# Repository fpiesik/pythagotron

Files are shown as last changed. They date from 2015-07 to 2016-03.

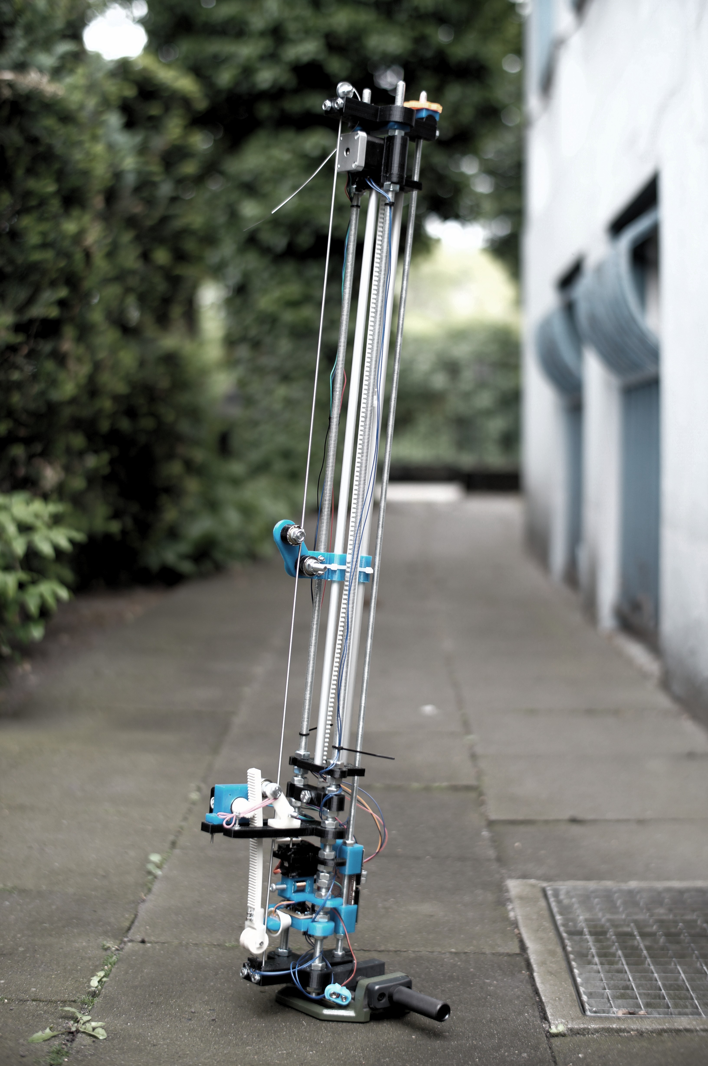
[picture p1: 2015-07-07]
doc/pictures/Pythagotron.jpg

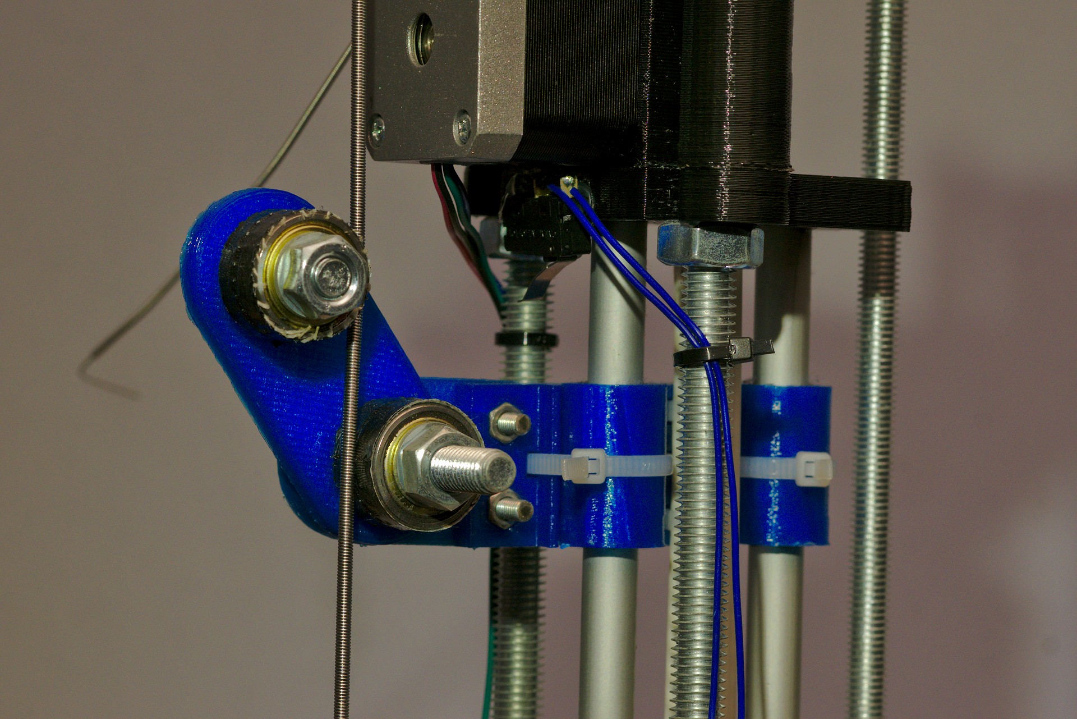
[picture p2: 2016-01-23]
doc/pictures/DSC03743.jpg

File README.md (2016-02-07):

Pythagoras of Samos was a man with many hobbys. I know him primarily for his experiments with strings and their musical properties. Thats why I call this robotic string instrument “Pythagotron”.

It features:

-2 octaves of pitch range
-fast and precise intonation
-4 actuators for striking, muting, punshing, damping and shorten the string
-modular and parametric design (OpenScad)
-most parts are 3D-printed or easy to gather
-open source

It's a parametric design made with OpenScad. You can view all the pieces put together by opening the file /print/pythagotron.scad. This preview differs a little from the actual way I put it together (see pictures).
To change the parameters, open /print/configuration.scad. You can also view or export every single piece by opening the corresponding .scad file and uncomment the module at the end of the file.

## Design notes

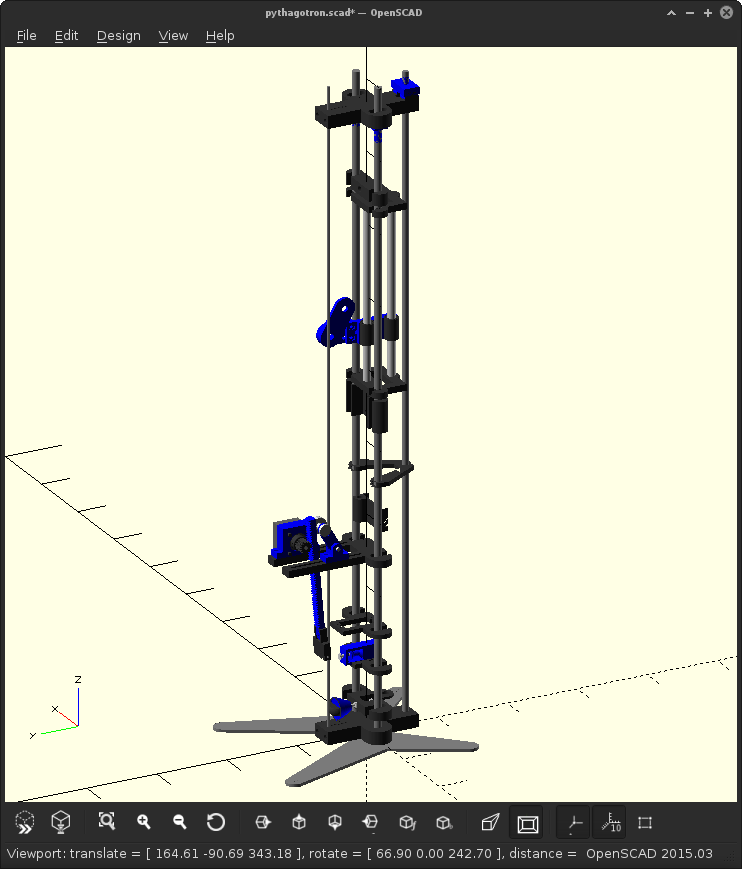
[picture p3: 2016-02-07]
doc/pictures/Screenshot_2016-01-23_19-48-24.png

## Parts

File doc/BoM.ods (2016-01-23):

Type | Specs | quant | price | Comment | Link
Frame
threaded rod | h=1m Ø=10mm | 2
threaded rod | h=1m Ø=8 | 1
threaded rod | h=14cm Ø=6mm | 4
rod | h=64cm Ø=10mm | 2
linear bearing | Ø=10 h=29mm | 2 |  | also available as printed part | http://www.igus.de/wpck/2292/drylin_r_rjum_01?ArtNr=RJUM-01-10&WT.mc_id=gadplDE022
bearing | Øi=8 Øo=22mm 608 Z (skateboard) | 6
Stepper motor | Nema17 | 1 |  |  | http://www.ebay.de/itm/DE-Ship-Nema-17-Schrittmotore-Stepper-Motor-Bipolar-59Ncm-CNC-3D-Printer-Reprap-/331440962687
Stepper motor | Nema14 | 1 |  |  | http://www.ebay.de/itm/Nema-14-Step-Motor-12V-0-4A-14Ncm-20oz-in-35x35x26mm-1-8deg-Bipolar-4-wire-/262038473998
Belt | T5 | ~2m |  |  | http://www.ebay.de/itm/Reprap-CNC-T5-PU-Zahnriemen-mit-Stahlzugstrang-T5-open-belt-/291357279515
Mainboard
Arduino nano |  | 1
Stepper motor driver | pololu a4988 or silent step stick (better) | 2 |  |  | http://www.watterott.com/de/SilentStepStick
DC-Converter | step down , 20V → 5-6V | 1 |  |  | http://www.ebay.de/itm/DC-DC-Schaltregler-Abwartswandler-LM2596HVS-4-5-53V-2A-step-down-converter-/321837441646
Power Jack | 5,5 mm / 2,1 mm | 1 |  |  | https://www.conrad.de/de/niedervolt-steckverbinder-buchse-einbau-horizontal-63-mm-21-mm-cliff-dc-10a-1-st-735742.html
Circuit Board | 100mm*50mm | 1 |  |  | https://www.conrad.de/de/basismaterial-fotobeschichtung-ohne-einseitig-35-m-l-x-b-100-mm-x-50-mm-106050-0100-proma-1-st-528200.html
Servo | standard | 1 |  |  | http://www.conrad.de/ce/de/product/275462/Bluebird-Standard-Servo-BMS-620-MG-Doppelt-kugelgelagert-Getriebe-Metall-JR
Mosfet | irf3205 | 2
Diode | 1n4001 | 2 |  |  | https://www.conrad.de/de/diode-1n4001-50v1a-diotec-1n4001-gehaeuseart-do-41-i-f-1-a-sperrspannung-u-r-50-v-162213.html
Kickup
copper wire | Coatet, Ø0,2mm | ~2m
Magnet | Neodym, Ø=5mm, h=min.20mm |  |  |  | https://www.conrad.de/de/piezokeramische-schallwandler-ft-serie-30-vac-4-05-khz-inhalt-1-st-710281.html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
 |  | 1 |  |  | http://www.supermagnete.de/stabmagnete-neodym-rund/stabmagnet-durchmesser-5mm-hoehe-25mm-neodym-n45-vernickelt_S-05-25-N
Preamp
opamp | tl081 | 1
trimpot
piezo | Ø27mm
Power Supply | ~20V, ~45W |  |  |  | https://www.conrad.de/de/notebook-netzteil-basetech-btna-90-90-w-15-vdc-16-vdc-195-vdc-462-a-1181511.html
Sring | Ø~0.1” (Low E-Bass-String) | 1

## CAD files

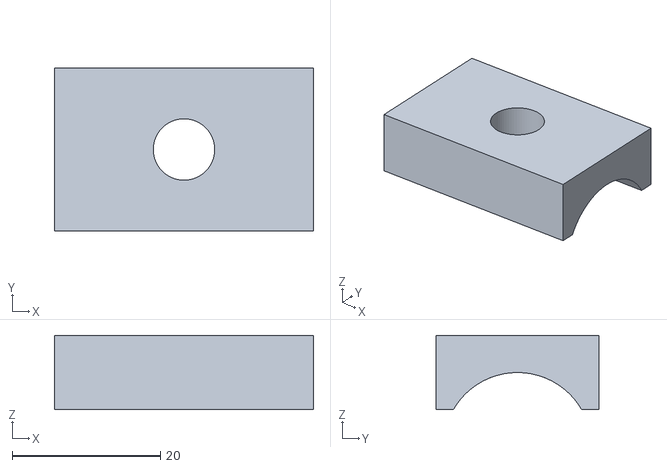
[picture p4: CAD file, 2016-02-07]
print/stls/tunerodfix.stl
35.0 x 22.0 x 10.0

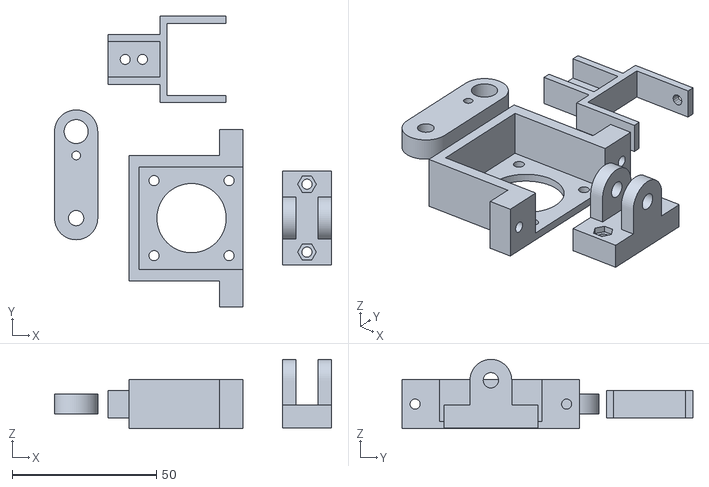
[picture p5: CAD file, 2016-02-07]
print/stls/damperB.stl
96.0 x 100.8 x 24.0

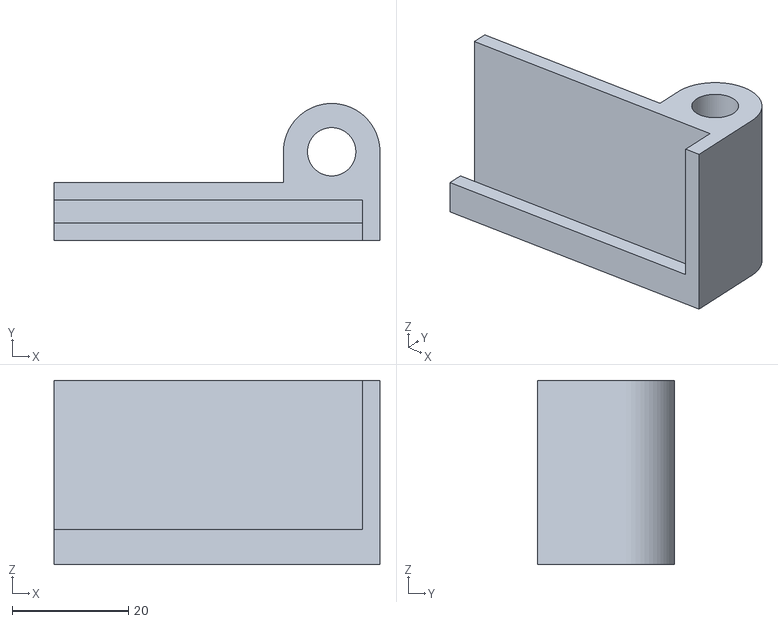
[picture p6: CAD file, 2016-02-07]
print/stls/pcb_mountA.stl
56.0 x 23.6 x 31.7

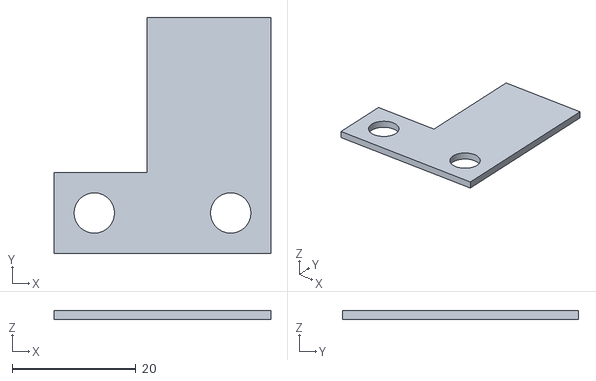
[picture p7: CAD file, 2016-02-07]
print/stls/endstop_mountB.stl
35.0 x 38.0 x 1.50

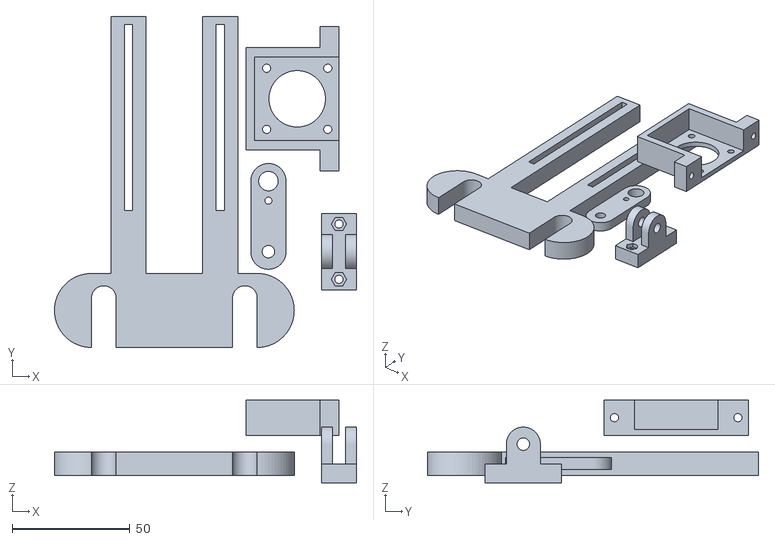
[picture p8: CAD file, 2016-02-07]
print/stls/damper.stl
128.5 x 140.8 x 35.2

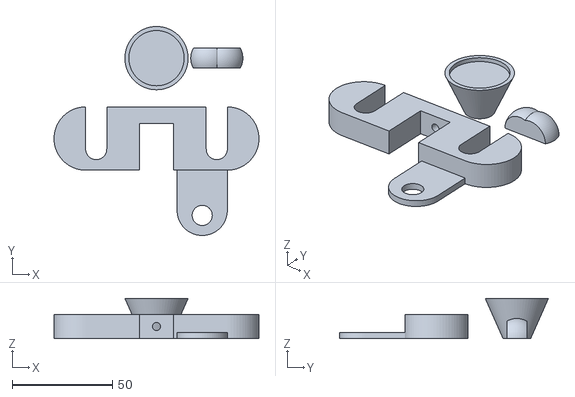
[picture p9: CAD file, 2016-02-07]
print/stls/piezo_pickup.stl
102.0 x 104.0 x 20.0

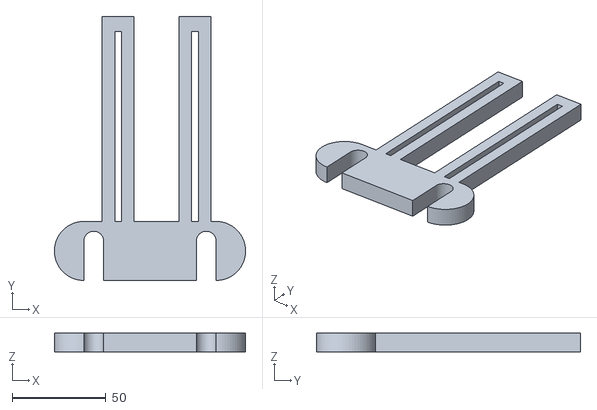
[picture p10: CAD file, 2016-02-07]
print/stls/damperA.stl
102.0 x 140.8 x 10.0

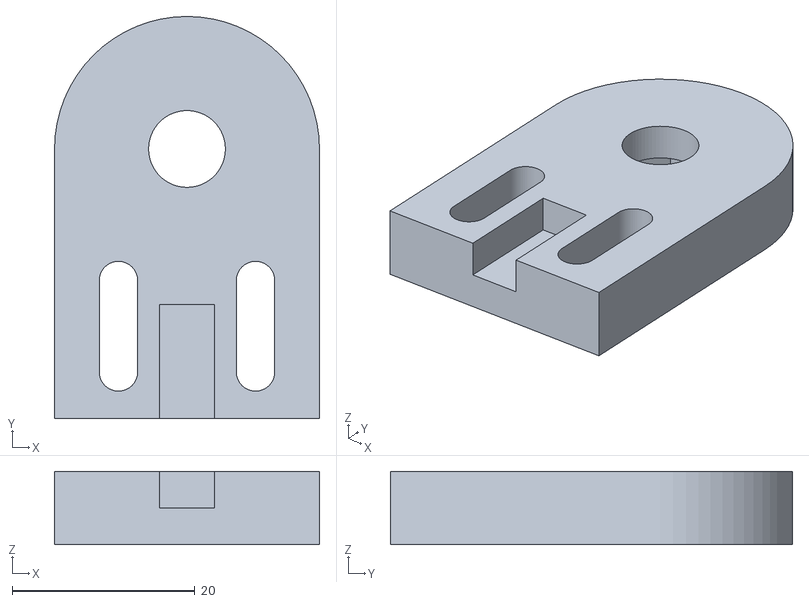
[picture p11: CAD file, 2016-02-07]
print/stls/stringshorter_armA.stl
29.0 x 44.0 x 8.00

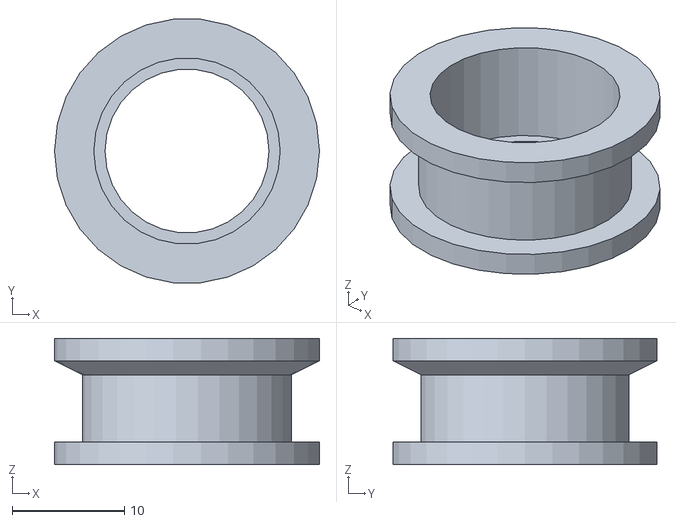
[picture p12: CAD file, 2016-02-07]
print/stls/pulleyB.stl
23.6 x 23.5 x 11.2

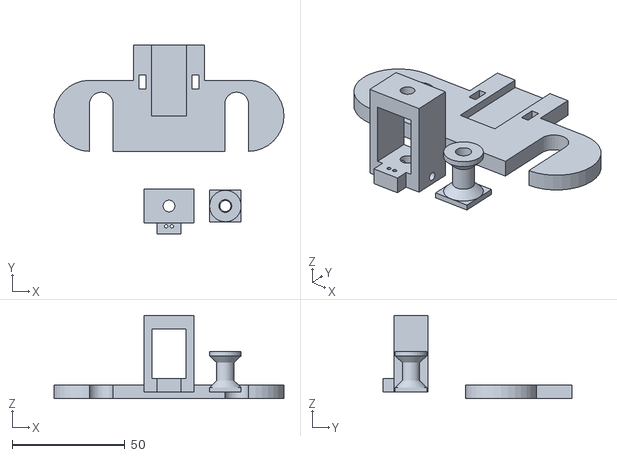
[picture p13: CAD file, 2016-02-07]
print/stls/kickup.stl
102.0 x 84.0 x 37.0

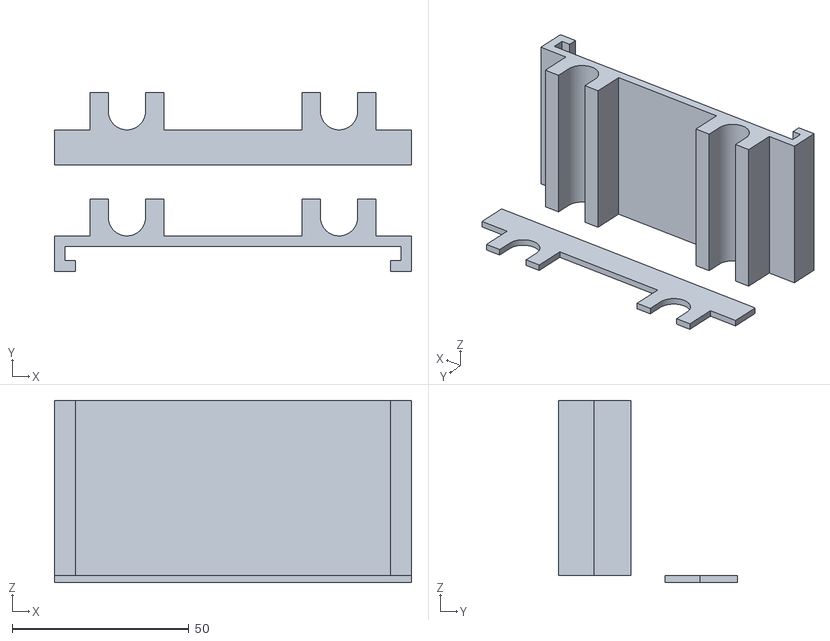
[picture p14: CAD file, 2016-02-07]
print/stls/pcb_mount.stl
101.0 x 50.5 x 51.5

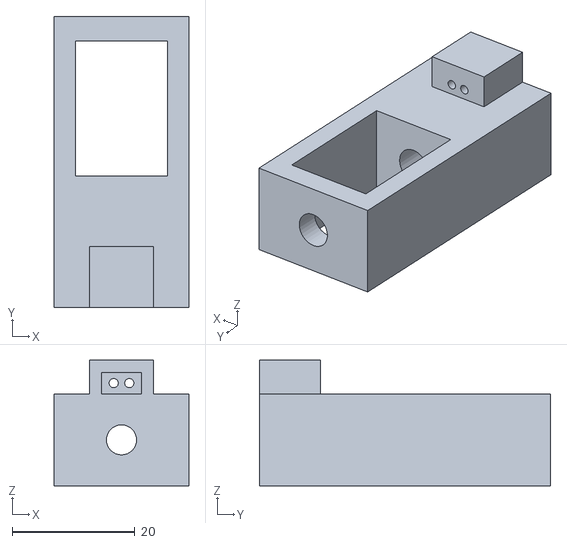
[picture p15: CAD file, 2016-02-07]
print/stls/kickup_A.stl
22.0 x 47.5 x 20.5

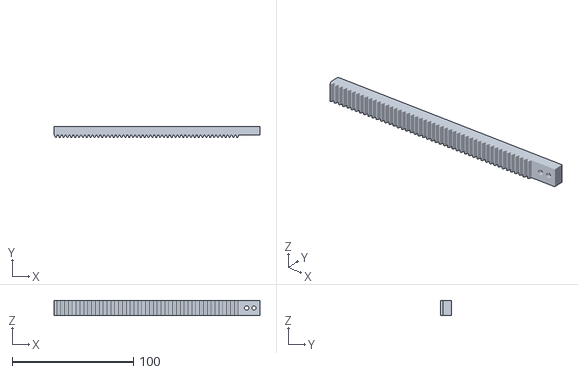
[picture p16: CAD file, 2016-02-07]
print/stls/damperC.stl
170.0 x 9.21 x 12.0

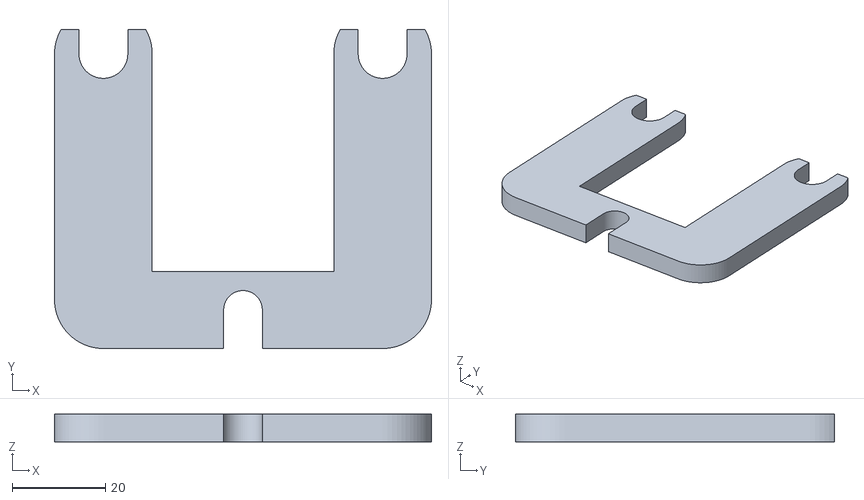
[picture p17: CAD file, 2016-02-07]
print/stls/spacer.stl
81.0 x 68.5 x 6.00

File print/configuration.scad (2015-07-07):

//Global variables: roddia, tunerodia, roddistance, screedlength, railroddia,stringholes


height=900; //overall height
roddia=10.5; //diameter of the main two rods
roddistance=60; //distance of the main two rods
tuneroddia=8.3; //diameter of the tunerod


pivotdia=20;
screedlength=130;
screedwidth=35;
screedheight=18;
stringroddist=screedlength-pivotdia;
stringdia=3.5;
stiffroddia=6.5;
pivotoffset=0;
stringholenumber=6;
stringholespread=5;

railrodZdist=20;
raildistance=35;
raildia=10.3;
railZ=250;



$fn=64;



basecolor=[0.2,0.2,0.2];    
actcolor=[0,0,1];

rodcolor=[0.5,0.5,0.5];
railcolor=[0.8,0.8,0.8];
boltcolor=[0.8,0.8,0.8];

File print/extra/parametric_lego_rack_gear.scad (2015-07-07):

width_in_studs  = 1;
teeth=48;
length= 170;
brick_height=7;
pocketZ=3.5;
screw_dia=3.5;
screw_posX=165;
screw_dist=6;

filz_mountX=18;
filz_dia=24;
filz_width=25;

  
  brick_width         = 12;
  stud_diameter       = 4.88;
 
  tooth_base_width    = 2.3;
  tooth_tip_width     = 0.87;
  tooth_height        = 2.06;
  tooth_top           = 5.79;
  tooth_tip_radius    = 0.15;
  teeth_per_brick     = 3.1;
  half_pegs_per_brick = 2;
  gap_width           = 0.884;



module tooth() {
  $fn = 20;
  

  //render()
  x_a = -((tooth_tip_width/2) - tooth_tip_radius);
  x_b = (tooth_tip_width/2) - tooth_tip_radius;
  translate([(gap_width+tooth_base_width)/2,0,-tooth_height+brick_height])
  rotate([0,0,180])
  translate([0,-(brick_width * width_in_studs)/2,tooth_height]) {
    difference() {
      hull() {
        translate([x_a,0,tooth_height]) rotate([90,0,0]) cylinder(r=tooth_tip_radius,   h=(brick_width * width_in_studs), center=true);
        translate([x_b,0,tooth_height]) rotate([90,0,0]) cylinder(r=tooth_tip_radius,   h=(brick_width * width_in_studs), center=true);
        translate([0,0,0])              rotate([90,0,0]) cylinder(r=tooth_base_width/2, h=(brick_width * width_in_studs), center=true);
      }
      translate([0,0,-1]) cube(size=[gap_width + tooth_base_width, brick_width * width_in_studs + 1, 1.9], center=true);
    }
  }
}

module rack() {
   wall_thickness      = 2;
difference(){
union(){
  tooth_width = tooth_base_width + gap_width;
  
 
  for ( i = [0 : teeth-1]) {
    translate([i * (tooth_base_width + gap_width), 0, 0]) tooth();
  }

  difference() {
    cube(size=[(length), (brick_width * width_in_studs), brick_height]);
    translate([wall_thickness,wall_thickness,0]) cube(size=[length - (wall_thickness*2), (brick_width * width_in_studs) - (wall_thickness*2), pocketZ]);
    // shave a bit off the beginning and end of the brick
    translate([-1.98,-1,0]) cube(size=[2, (brick_width * width_in_studs)+2, 10]);
    translate([length - 0.02,-1,0]) cube(size=[2,length+2, 10]);
  }

 }

translate([screw_posX,brick_width/2,0])cylinder(d=screw_dia, h=brick_height+1,$fn=16);
translate([screw_posX-screw_dist,brick_width/2,0])cylinder(d=screw_dia, h=brick_height+1,$fn=16);
}
}

module filz_mount(){
    wall_thickness      = 2.5;
    tolerance=0.3;
    height=brick_height+wall_thickness;
    block_rackY=filz_dia/2+3*wall_thickness+screw_dia;
    block_filzX=filz_dia/2+3*wall_thickness+screw_dia;
    block_filzY=filz_width+2*wall_thickness;
difference(){    
union(){
difference(){
cube([filz_mountX,brick_width+2*wall_thickness+tolerance,height],center=true);
translate([0,0,wall_thickness])cube([filz_mountX,brick_width+tolerance,height],center=true);    
}
difference(){
translate([filz_mountX/2+ block_filzX/2,0,0])cube([block_filzX,block_filzY,brick_height+wall_thickness],center=true); 
translate([filz_mountX/2+ block_filzX/2+wall_thickness,0,0])cube([block_filzX,filz_width,brick_height+wall_thickness],center=true); 
    }
}
translate([screw_dist/2,0,0])cylinder(d=screw_dia, h=brick_height+wall_thickness+1,$fn=16,center=true);
translate([-screw_dist/2,0,0])cylinder(d=screw_dia, h=brick_height+wall_thickness+1,$fn=16,center=true);
translate([filz_mountX/2+block_filzX-screw_dia/2-wall_thickness,0,0])rotate([90,0,0])cylinder(d=screw_dia, h=filz_width+2*wall_thickness+1,$fn=16,center=true);
}
}

//rack();
filz_mount();

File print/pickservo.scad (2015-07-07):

include <configuration.scad>;

module pickservo_mount(){

height=6;
depth=roddia*3;
width=roddistance+roddia;
screwdia=3;
screwnumber=2; //one or two screws
screwdistance=10; //if two screws
servowidth=40.5;
servodepth=20.5;
servosupportX=8;
servosupportY=8;

cable_cutoutX=5;
cable_cutoutY=3;

offsetY=15;

rotate([0,0,0]){
difference(){
union(){


cube([width,depth,height],center=true);
translate([width/2,0,0]){
cylinder(d=depth,h=height,center=true);}
translate([-width/2,0,0]){
cylinder(d=depth,h=height,center=true);}
translate([0,offsetY,0]){
cube([servodepth+servosupportX*2,servowidth+servosupportY*2,height],center=true);
}}
translate([0,offsetY,0]){
cube([servodepth,servowidth,height+1],center=true);
cube([cable_cutoutX,servowidth+cable_cutoutY*2,height+1],center=true);

if (screwnumber==1){
translate([0,servowidth/2+servosupportY/2,0]){
cylinder(d=screwdia,h=height+1,center=true);}
translate([0,-(servowidth/2+servosupportY/2),0]){
cylinder(d=screwdia,h=height+1,center=true);}
}

if (screwnumber==2){
translate([screwdistance/2,0,0]){
translate([0,servowidth/2+servosupportY/2,0]){
cylinder(d=screwdia,h=height+1,center=true);}
translate([0,-(servowidth/2+servosupportY/2),0]){
cylinder(d=screwdia,h=height+1,center=true);}
}
translate([-screwdistance/2,0,0]){
translate([0,servowidth/2+servosupportY/2,0]){
cylinder(d=screwdia,h=height+1,center=true);}
translate([0,-(servowidth/2+servosupportY/2),0]){
cylinder(d=screwdia,h=height+1,center=true);}
}
}

}

translate([0,depth/2-roddia,0]){
translate([roddistance/2,0,0]){
cylinder(d=roddia,h=height+1,center=true);}
translate([-roddistance/2,0,0]){
cylinder(d=roddia,h=height+1,center=true);}

translate([roddistance/2,-depth/2,0]){
cube([roddia,depth,roddia],center=true);}
translate([-roddistance/2,-depth/2,0]){
cube([roddia,depth,roddia],center=true);}
}

}

}
}
//servo_mount();

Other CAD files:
print/stls/rail_mount.stl
print/stls/pcb_mountB.stl
print/stls/picker.stl
print/stepper_mount.scad
print/damper.scad
print/endmounts.scad
print/endstop_mount.scad
print/extra/bearing.scad
print/extra/bolt_nut.scad
print/extra/legopulley.scad
print/extra/linear_bearing.scad
print/extra/nema.scad
print/extra/pulleyA.scad
print/extra/pulleyB.scad
print/extra/rack_gear.scad
print/kickup.scad
print/pcb_mount.scad
print/pick.scad
print/picker.scad
print/pickup_mag.scad
print/piezo_pickup.scad
print/pulley_mount.scad
print/pythagotron.scad
print/rack_gear.scad
print/rail_mount.scad
print/spacer.scad
print/stand.scad
print/stls/endstop_mount.stl
print/stls/kickup_C.stl
print/stls/kickup_D.stl
print/stls/pivot.stl
print/stls/pulleyA.stl
print/stls/pulleymount.stl
print/stls/screedA.stl
print/stls/screedB.stl
print/stls/stand.stl
print/stls/steppermountA.stl
print/stls/stringshorter.stl
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

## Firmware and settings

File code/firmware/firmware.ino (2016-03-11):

#include <Servo.h>
Servo servo1;
Servo servo2;

const int home1_pin = 13;  //Digital input 1
const int home2_pin = 12;  //Digital input 2

//-------choose hardware---------------------
//uncomment if Hardware V1
const int analogAux1_pin = A6;
const int analogAux2_pin = A7;
const int step1_stpPin = 3;
const int step1_dirPin = 2;
const int step1_enblPin = 4;
const int step2_stpPin = 6; 
const int step2_dirPin = 5;
const int step2_enblPin = 7;

//uncomment if hardware V2
//const int analogAux1_pin = A0;// A6 Hardware ref1
//const int analogAux2_pin = A1;// A7  "
//const int step1_stpPin = 3;
//const int step1_dirPin = 4; 
//const int step1_enblPin = 2;
//const int step2_stpPin = 6;
//const int step2_dirPin = 7;  
//const int step2_enblPin = 5; 
//--------------------------------------------

const int mosfet1_pin = 10; 
const int mosfet2_pin = 11;

const int servo1Pin = 9;
const int servo2Pin = 8;



bool step1_enbl=0;
int step1_maxSpd = 240; 
int step1_homeSpd = 800; 
long step1_startSpd = 10000;
long step1_brkSteps = 100;
int step1_rampAmnt = 5;
bool step1_rmpDwn = 0;
bool step1_rmpUp = 0;
int step1_trgtSpd = 1500;
byte step1_dir = 0;
byte step1_move = 0;
long step1_pos=0;
long  step1_trgt;
long step1_prevTrgt;
long step1_trgtA;
long step1_trgtB;
bool step1_arrvd=1;
long step1_interval = 1000; 
unsigned long step1_prvMilli = 0; 
byte step1_homeState = 1;
byte step1_arriving=0;
long step1_prevPos;


bool step2_enbl=0;
int step2_maxSpd = 240; 
int step2_homeSpd = 1200; 
long step2_startSpd = 5000;
long step2_brkSteps = 50;
int step2_rampAmnt = 5;
bool step2_rmpDwn = 0;
bool step2_rmpUp = 0;
int step2_trgtSpd = 1500;
byte step2_dir = 0;
byte step2_move = 0;
long step2_pos=0;
long  step2_trgt;
long step2_prevTrgt;
long step2_trgtA;
long step2_trgtB;
bool step2_arrvd=1;
long step2_interval = 1000; 
unsigned long step2_prvMilli = 0; 
byte step2_homeState = 1;
byte step2_arriving=0;
long step2_prevPos;


unsigned int kick1_duration;
unsigned long kick1_prvMilli = 0;
unsigned long kick1_currMilli = 0;  

unsigned int kick2_duration;
unsigned long kick2_prvMilli = 0;
unsigned long kick2_currMilli = 0;  

int servo1_strtPos = 90;
int servo2_strtPos = 90;


byte serbyte = 0;
byte incoming = 0;





void step_home(byte stepper){
  byte home_pin;
  byte enbl_pin;
  byte dir_pin;
  byte stp_pin;
  int home_spd;
  
    
  if (stepper==1){
    home_pin= home1_pin;
    enbl_pin = step1_enblPin;
    dir_pin = step1_dirPin;
    stp_pin = step1_stpPin;
    home_spd = step1_homeSpd;
    step1_pos=0;
     
  }
  
   if (stepper==2){
    home_pin= home2_pin;
    enbl_pin = step2_enblPin;
    dir_pin = step2_dirPin;
    stp_pin = step2_stpPin;
    home_spd = step2_homeSpd;
    step2_pos=0;
 
  }
  
  stepDir(stepper,1); 
  
      
  while (digitalRead(home_pin)==1){
  digitalWrite(enbl_pin, LOW);
  digitalWrite(stp_pin, HIGH);
  delayMicroseconds(10);
  digitalWrite(stp_pin,LOW);
  delayMicroseconds(home_spd-10);
  }
  //digitalWrite(enblPin, HIGH);
  //digitalWrite(enbl_pin, HIGH);
  stepSndpos(stepper);
  
}





void mosfet(byte mosfet,byte time){
  if(mosfet==1){
  digitalWrite (mosfet1_pin,HIGH);
  kick1_prvMilli = kick1_currMilli;  
  kick1_duration = time;
  } 
   if(mosfet==2){
  digitalWrite (mosfet2_pin,HIGH);
  kick2_prvMilli = kick2_currMilli;  
  kick2_duration = time;
  } 
}

//------------------------------------------------------------------------    
void stepEnbl(byte stepper,int state){
 byte enbl_pin;
 
 if (stepper==1) enbl_pin=step1_enblPin;
 if (stepper==2) enbl_pin=step2_enblPin;
 
 int statePin=state*-1+1;
 digitalWrite(enbl_pin, statePin);
 
 if (stepper==1)  step1_enbl=state;
 if (stepper==2)  step2_enbl=state;
 delayMicroseconds(50);
}

//------------------------------------------------------------------------
void stepDir(byte stepper,byte dir){
  byte step_dir;
  byte dir_pin;
  
  if (stepper == 1){
  step_dir=step1_dir;
  dir_pin = step1_dirPin;
  }
  if (stepper == 2){
  step_dir=step2_dir;
  dir_pin = step2_dirPin;
  }
  if(step_dir!=dir){
  digitalWrite(dir_pin, dir);
  
  
  if (stepper==1)step1_dir=dir;
  if (stepper==2)step2_dir=dir;
  delayMicroseconds(2); 
  }
}
//-------------------------------------------------------------------------
void step_setSpd(byte stepper,long spd){
  if(stepper==1){
    step1_trgtSpd= step1_maxSpd+100*step1_startSpd/(spd+100)-100*step1_startSpd/300;
    step1_rmpUp=1;
    
  }
  
  if(stepper==2){
    step2_trgtSpd= step2_maxSpd+100*step2_startSpd/(spd+100)-100*step2_startSpd/300;
    step2_rmpUp=1;
   }
   
   
}
//-------------------------------------------------------------------------
void stepSndpos(byte stepper){
  long step_pos;
  
  if(stepper==1)step_pos=step1_pos;
  if(stepper==2)step_pos=step2_pos;
  
  long pos1=step_pos/1000;
  long pos2=(step_pos-pos1*1000)/10;
  long pos3=step_pos-pos1*1000-pos2*10;
  if(stepper==1)Serial.write(255);
  if(stepper==2)Serial.write(254);
  Serial.write(pos1);
  Serial.write(pos2);
  Serial.write(pos3);
}


//-------------------------------------------------------------------------
void stepMove(byte stepper){
  
unsigned long prvMilli;
long interval;
byte stp_pin;
byte dir;
long pos;
long prev_pos;
long trgt;
int brkSteps;
byte rmpUp;
byte rmpDwn;
byte arriving;
int trgtSpd;
long startSpd;

if (stepper==1){
  prvMilli=step1_prvMilli;
  interval=step1_interval;
  stp_pin=step1_stpPin;
  dir=step1_dir;
  pos=step1_pos;
  trgt=step1_trgt;
  brkSteps=step1_brkSteps;
  rmpUp=step1_rmpUp;
  rmpDwn=step1_rmpDwn;
  arriving=step1_arriving;
  prev_pos=step1_prevPos;
  trgtSpd=step1_trgtSpd;
  startSpd=step1_startSpd;
  
}

if (stepper==2){
  prvMilli=step2_prvMilli;
  interval=step2_interval;
  stp_pin=step2_stpPin;
  dir=step2_dir;
  pos=step2_pos;
  trgt=step2_trgt;
  brkSteps=step2_brkSteps;
  rmpUp=step2_rmpUp;
  rmpDwn=step2_rmpDwn;
  arriving=step2_arriving;
  prev_pos=step2_prevPos;
  trgtSpd=step2_trgtSpd;
  startSpd=step2_startSpd;
}
  
  unsigned long currentMillis = micros();
  if(currentMillis - prvMilli >= interval) {
      
  digitalWrite(stp_pin, HIGH);
  delayMicroseconds(4);
  digitalWrite(stp_pin,LOW);
  if(dir==0)pos=pos+1;
  if(dir==1)pos=pos-1;
  if((sqrt(pow(pos - trgt,2))<brkSteps) && (sqrt(pow(pos - trgt,2))<sqrt(pow(prev_pos - trgt,2)))){
  interval = interval + 2*brkSteps / sqrt(pow(pos - trgt,2));
  //stepRmpdwn(stepper,(startSpd-trgtSpd)/brkSteps);
  arriving=1;}  
  
  prev_pos=pos;
  
  if (stepper==1){
  step1_prvMilli = currentMillis; 
  step1_pos=pos;
  step1_prevPos=prev_pos;
  step1_arriving=arriving;
  step1_interval=interval;
  }
  if (stepper==2){
  step2_prvMilli = currentMillis; 
  step2_pos=pos;
  step2_prevPos=prev_pos;
  step2_arriving=arriving;
  step2_interval=interval;
  }

  }
  
  
}
//--------------------------------------------------------------------------
void stepGo2pos(byte stepper){
  long trgt;
  long prevTrgt;
  byte trgtA;
  byte trgtB;
  byte rmpUp;
  byte rmpDwn;
  long pos;
  bool arrvd;
 
 
 if(stepper==1){
  trgt=step1_trgt;
  prevTrgt=step1_prevTrgt;
  trgtA=step1_trgtA;
  trgtB=step1_trgtB;
  rmpUp=step1_rmpUp;
  rmpDwn=step1_rmpDwn;
  pos=step1_pos;
  arrvd=step1_arrvd;
  
 }
  if(stepper==2){
  trgt=step2_trgt;
  prevTrgt=step2_prevTrgt;
  trgtA=step2_trgtA;
  trgtB=step2_trgtB;
  rmpUp=step2_rmpUp;
  rmpDwn=step2_rmpDwn;
  pos=step2_pos;
  arrvd=step2_arrvd;
 }
 
  
  rmpUp=1;
  trgt=trgtA*100+trgtB;
  if (trgt!=pos) {
  arrvd=0;
  
  if(prevTrgt>pos && trgt<pos)rmpDwn=1;
  if(prevTrgt<pos && trgt>pos)rmpDwn=1;
  
  prevTrgt=trgt;}
  
  if(stepper==1){
  step1_trgt=trgt;  
  step1_prevTrgt=prevTrgt;
  step1_rmpUp=rmpUp;
  step1_rmpDwn=rmpDwn;
  step1_arrvd=arrvd;
  step1_arriving=0;
  }
   if(stepper==2){
  step2_trgt=trgt;
  step2_prevTrgt=prevTrgt;
  step2_rmpUp=rmpUp;
  step2_rmpDwn=rmpDwn;
  step2_arrvd=arrvd;
  step2_arriving=0;
  }
  
}
//------------------------------------------------------------------------------
void stepRmpdwn(byte stepper,int amount){
  long startSpd;
  long interval;
  byte rmpDwn;
   
  if (stepper==1) {
  startSpd=step1_startSpd;
  interval=step1_interval;
  rmpDwn=step1_rmpDwn;
  }
  
  if (stepper==2) {
  startSpd=step2_startSpd;
  interval=step2_interval;
  rmpDwn=step2_rmpDwn;
  }
  
  if(startSpd>interval)interval=interval+amount;
  if(startSpd<interval)interval=interval-amount;
  if(startSpd<=interval+amount && startSpd>=interval-amount)rmpDwn=0;
  
  if (stepper==1){
  step1_rmpDwn=rmpDwn;
  step1_interval=interval;
  }
  if (stepper==2){
  step2_rmpDwn=rmpDwn;
  step2_interval=interval;
  }
  
  
  
  
  }

//--------------------------------------------------------------------------------
void stepRmpup(byte stepper){
  
  int trgtSpd;
  long interval;
  int rampAmnt;
  byte rmpUp;
  byte arriving;
   
  if (stepper==1) {
  trgtSpd=step1_trgtSpd;
  interval=step1_interval;
  rampAmnt=step1_rampAmnt;
  rmpUp=step1_rmpUp;
  arriving=step1_arriving;
  }
   if (stepper==2) {
  trgtSpd=step2_trgtSpd;
  interval=step2_interval;
  rampAmnt=step2_rampAmnt;
  rmpUp=step2_rmpUp;
  arriving=step2_arriving;
  }
  
  if(rmpUp==1 && arriving==0){
  if(trgtSpd>interval)interval=interval+rampAmnt;
  if(trgtSpd<interval)interval=interval-rampAmnt;}
  if(trgtSpd<=interval+rampAmnt && trgtSpd>=interval-rampAmnt)rmpUp=0;
  
  if (stepper==1){
  step1_rmpUp=rmpUp;
  step1_interval=interval;}
  
  if (stepper==2){
  step2_rmpUp=rmpUp;
  step2_interval=interval;}
  
}

void setServo(byte servo,byte pos){
if (servo==1 && pos!=0){
  servo1.attach(servo1Pin);
  servo1.write(pos);
 }
if (servo==2 && pos!=0){
  servo2.attach(servo2Pin);
  servo2.write(pos);
 }

 if (servo==1 && pos==0) servo1.detach();
 if (servo==2 && pos==0) servo2.detach();
 
}

void setup() 
{                
  Serial.begin(115200);
  pinMode(home1_pin, INPUT);
  
  pinMode(step1_stpPin, OUTPUT);
  pinMode(step1_dirPin, OUTPUT);
  pinMode(step1_enblPin, OUTPUT);
  
  pinMode(step2_stpPin, OUTPUT);
  pinMode(step2_dirPin, OUTPUT);
  pinMode(step2_enblPin, OUTPUT);
  
  pinMode(mosfet1_pin, OUTPUT);
  pinMode(mosfet2_pin, OUTPUT);
  
  
  digitalWrite(home1_pin, HIGH);
  step1_homeState = digitalRead(home1_pin);
  
  digitalWrite(home2_pin, HIGH);
  step2_homeState = digitalRead(home2_pin);
  
  
  
  digitalWrite(step1_stpPin, LOW);
  digitalWrite(step1_dirPin, LOW);
  digitalWrite(step1_enblPin, HIGH);
  
  digitalWrite(step2_stpPin, LOW);
  digitalWrite(step2_dirPin, LOW);
  digitalWrite(step2_enblPin, HIGH);
  
  digitalWrite(mosfet1_pin, LOW);
  digitalWrite(mosfet2_pin, LOW);
  
  
  
  step_home(2);
  step_home(1);
  stepEnbl(1,0);
  
  
  
}


void loop() 
{
if (Serial.available()) {
       
        serbyte = Serial.read();
        //Serial.write(serbyte);
        if (serbyte > 200) incoming = serbyte - 200;
        if (serbyte <= 200){
            
            //Stepper1
            if (incoming == 1) step_home(1);
            if (incoming == 2) stepEnbl(1,serbyte);
            if (incoming == 3) step_setSpd(1,serbyte);
            if (incoming == 4) stepSndpos(1);
            if (incoming == 5) step1_trgtA=serbyte;
            if (incoming == 6) {step1_trgtB=serbyte; 
                                stepGo2pos(1);}
            //Stepper2 
            if (incoming == 7) step_home(2);
            if (incoming == 8) stepEnbl(2,serbyte);
            if (incoming == 9) step_setSpd(2,serbyte);
            if (incoming == 10) stepSndpos(2);
            if (incoming == 11) step2_trgtA=serbyte;
            if (incoming == 12) {step2_trgtB=serbyte; 
                                 stepGo2pos(2);}
              
              
            if (incoming == 13) setServo(1,serbyte);
            if (incoming == 14) setServo(2,serbyte);
            if (incoming == 15) mosfet(1,serbyte);
            if (incoming == 16) mosfet(2,serbyte);
            
            
        }  



}

//------------------------------------------------------------------------------

kick1_currMilli = millis();
   if(kick1_currMilli - kick1_prvMilli >= kick1_duration || mosfet1_pin==HIGH) {
   digitalWrite(mosfet1_pin, LOW);
  }
kick2_currMilli = millis();
   if(kick2_currMilli - kick2_prvMilli >= kick2_duration || mosfet2_pin==HIGH) {
   digitalWrite(mosfet2_pin, LOW);
  }

 
  
//-----------------------------------------------------------------------------  
 if(step1_arrvd==0 && step1_enbl==1){
   if (step1_pos<step1_trgt) {
     if(step1_rmpDwn==1)stepRmpdwn(1,step1_rampAmnt);
     if(step1_rmpDwn==0){
     stepDir(1,0); 
     stepRmpup(1);
   }
     step1_move=1;}
   if (step1_pos>step1_trgt) {
     if(step1_rmpDwn==1)stepRmpdwn(1,step1_rampAmnt);
     if(step1_rmpDwn==0){
     stepDir(1,1); 
     stepRmpup(1);
   }
     step1_move=1;}
   }
   if (step1_pos==step1_trgt && step1_arrvd==0){
     step1_move=0; 
     step1_arrvd=1;
     step1_arriving=0;
     stepSndpos(1);  
     } 
      
   
 if(digitalRead(home1_pin)==0)step1_pos=0;
 if (step1_move>0){
   //stepEnbl(1);
     if(step1_enbl==1);stepMove(1);
   }  
   if (step1_move==0){
     step1_interval=step1_startSpd;
     //stepEnbl(0);
   }
 


//-----------------------------------------------------------------------------  
 if(step2_arrvd==0 && step2_enbl==1){
   if (step2_pos<step2_trgt) {
     if(step2_rmpDwn==1)stepRmpdwn(2,step2_rampAmnt);
     if(step2_rmpDwn==0){
     stepDir(2,0); 
     stepRmpup(2);
   }
     step2_move=1;}
   if (step2_pos>step2_trgt) {
     if(step2_rmpDwn==1)stepRmpdwn(2,step2_rampAmnt);
     if(step2_rmpDwn==0){
     stepDir(2,1); 
     stepRmpup(2);
   }
     step2_move=1;}
   }
   if (step2_pos==step2_trgt && step2_arrvd==0){
     step2_move=0; 
     step2_arrvd=1;
     step2_arriving=0;
     stepSndpos(1); 
     } 
      
   
 if(digitalRead(home2_pin)==0)step2_pos=0;
 if (step2_move>0){
   //stepEnbl(1);
     if(step2_enbl=1);stepMove(2);
     
 }  
   if (step2_move==0){
     step2_interval=step2_startSpd;
     //stepEnbl(0);
   }
 
}

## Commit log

2015-07-07 completed first design
    [BoM.ods, bearing.scad, bolt_nut.scad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]
2015-10-07 added endstop mount
    [endstop_mount.scad]
2016-01-23 added pictures
    [BoM.ods, damper.scad, kickup.scad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]
2016-02-07 added STLs and audio examples
    [damper.stl, damperA.stl, damperB.stl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]
2016-03-11 added function to switch servo off after 5 seconds of inactivity
2016-03-11 don't activate servo on startup
2016-03-11 changed max stepper speed
